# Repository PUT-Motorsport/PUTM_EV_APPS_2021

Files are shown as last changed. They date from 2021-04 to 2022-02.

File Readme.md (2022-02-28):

# Accelerator Pedal Position Sensor (APPS)

## Motivation

APPS handling is required by official FSG Rules according to T11.8 ([see](https://www.formulastudent.de/fileadmin/user_upload/all/2022/rules/FS-Rules_2022_v1.0.pdf#page=58)). APPS signals are system critical signals meaning that any implausibility between sensors or a failure should result in complete motor power shutdown.

## Pedal travel

* 0% - fully released
* 100% - fully applied

## Implausiblity

Implausibility is defined as a deviation of more than ten percentage points pedal travel
between any of the used APPSs. If it occurs for more than 100 ms the power to the motor must be immediately shut down.

## Platform

Software for APPS signal handling is developed using C++ for STM32 microcontroller.

## Program schematic

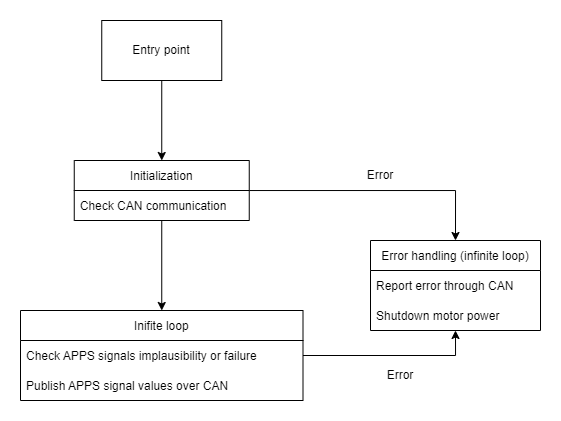
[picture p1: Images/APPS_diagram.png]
APPS diagram


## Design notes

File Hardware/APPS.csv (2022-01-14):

"Source:,""C:\Users\Patryk\Desktop\PUTM\APPS\PUTM_EV_APPS_2021\Hardware\APPS.kicad_sch"""
"Date:,""13.01.2022 20:09:16"""
"Tool:,""Eeschema (6.0.0)"""
"Generator:,""D:\KiCad\6.0\bin\scripting\plugins/bom_csv_grouped_by_value.py"""
"Component Count:,""62"""
Individual Components:
"Item,""Qty"",""Reference(s)"",""Value"",""LibPart"",""Footprint"",""Datasheet"""
","""",""C1"",""100nF"",""Device:C"",""Capacitor_SMD:C_0603_1608Metric_Pad1.08x0.95mm_HandSolder"",""~"""
","""",""C2"",""100nF"",""Device:C"",""Capacitor_SMD:C_0603_1608Metric_Pad1.08x0.95mm_HandSolder"",""~"""
","""",""C3"",""100nF"",""Device:C"",""Capacitor_SMD:C_0603_1608Metric_Pad1.08x0.95mm_HandSolder"",""~"""
","""",""C4"",""100nF"",""Device:C"",""Capacitor_SMD:C_0603_1608Metric_Pad1.08x0.95mm_HandSolder"",""~"""
","""",""C5"",""100nF"",""Device:C"",""Capacitor_SMD:C_0603_1608Metric_Pad1.08x0.95mm_HandSolder"",""~"""
","""",""C6"",""100nF"",""Device:C"",""Capacitor_SMD:C_0603_1608Metric_Pad1.08x0.95mm_HandSolder"",""~"""
","""",""C7"",""22pF"",""Device:C"",""Capacitor_SMD:C_0603_1608Metric_Pad1.08x0.95mm_HandSolder"",""~"""
","""",""C8"",""22pF"",""Device:C"",""Capacitor_SMD:C_0603_1608Metric_Pad1.08x0.95mm_HandSolder"",""~"""
","""",""C12"",""100nF"",""Device:C"",""Capacitor_SMD:C_0603_1608Metric_Pad1.08x0.95mm_HandSolder"",""~"""
","""",""C13"",""100nF"",""Device:C"",""Capacitor_SMD:C_0603_1608Metric_Pad1.08x0.95mm_HandSolder"",""~"""
","""",""C14"",""100nF"",""Device:C"",""Capacitor_SMD:C_0603_1608Metric_Pad1.08x0.95mm_HandSolder"",""~"""
","""",""C15"",""100nF"",""Device:C"",""Capacitor_SMD:C_0603_1608Metric_Pad1.08x0.95mm_HandSolder"",""~"""
","""",""C16"",""100nF"",""Device:C"",""Capacitor_SMD:C_0603_1608Metric_Pad1.08x0.95mm_HandSolder"",""~"""
","""",""C17"",""100nF"",""Device:C"",""Capacitor_SMD:C_0603_1608Metric_Pad1.08x0.95mm_HandSolder"",""~"""
","""",""C18"",""100nF"",""Device:C"",""Capacitor_SMD:C_0603_1608Metric_Pad1.08x0.95mm_HandSolder"",""~"""
","""",""C19"",""100n"",""Device:C"",""Capacitor_SMD:C_0603_1608Metric_Pad1.08x0.95mm_HandSolder"",""~"""
","""",""C20"",""100n"",""Device:C"",""Capacitor_SMD:C_0603_1608Metric_Pad1.08x0.95mm_HandSolder"",""~"""
","""",""D1"",""LED"",""Device:LED"",""LED_SMD:LED_0603_1608Metric_Pad1.05x0.95mm_HandSolder"",""~"""
","""",""D2"",""LED"",""Device:LED"",""LED_SMD:LED_0603_1608Metric_Pad1.05x0.95mm_HandSolder"",""~"""
","""",""D3"",""LED"",""Device:LED"",""LED_SMD:LED_0603_1608Metric_Pad1.05x0.95mm_HandSolder"",""~"""
","""",""D4"",""LED"",""Device:LED"",""LED_SMD:LED_0603_1608Metric_Pad1.05x0.95mm_HandSolder"",""~"""
","""",""D5"",""D_TVS"",""Device:D_TVS"",""Diode_SMD:D_0603_1608Metric_Pad1.05x0.95mm_HandSolder"",""~"""
","""",""D6"",""D_TVS"",""Device:D_TVS"",""Diode_SMD:D_0603_1608Metric_Pad1.05x0.95mm_HandSolder"",""~"""
","""",""D9"",""PESD2CAN.215"",""Device:D_TVS_x2_AAC"",""Package_TO_SOT_SMD:SOT-23"","""""
","""",""D10"",""DIODE"",""pspice:DIODE"",""Diode_SMD:D_SMB"",""~"""
","""",""F2"",""Fuse"",""Device:Fuse"",""Fuse:Fuse_2010_5025Metric"",""~"""
","""",""F3"",""Fuse"",""Device:Fuse"",""Fuse:Fuse_2010_5025Metric"",""~"""
","""",""J4"",""Sygnały"",""conn_02x20_odd_even:Conn_02x20_Odd_Even"",""Connector_PinSocket_2.54mm:PinSocket_2x20_P2.54mm_Vertical"","""""
","""",""J5"",""Diagnostyka"",""conn_02x10_odd_even:Conn_02x10_Odd_Even"",""Connector_PinSocket_2.54mm:PinSocket_2x10_P2.54mm_Vertical"","""""
","""",""J8"",""Zasilanie+CAN"",""conn_02x10_odd_even:Conn_02x10_Odd_Even"",""Connector_PinSocket_2.54mm:PinSocket_2x10_P2.54mm_Vertical"","""""
","""",""JP1"",""Jumper_NC_Small"",""Device:Jumper_NC_Small"",""Connector_PinHeader_2.54mm:PinHeader_1x02_P2.54mm_Vertical"","""""
","""",""K1"",""FINDER-30.22"",""Relay:FINDER-30.22"",""Relay_THT:Relay_DPDT_Finder_30.22"",""http://gfinder.findernet.com/assets/Series/354/S30EN.pdf"""
","""",""L1"",""10u"",""Device:L"",""Inductor_SMD:L_0805_2012Metric"",""~"""
","""",""Q1"",""BSS138"",""Transistor_FET:BSS138"",""Package_TO_SOT_SMD:SOT-23"",""https://www.fairchildsemi.com/datasheets/BS/BSS138.pdf"""
","""",""R1"",""10k"",""Device:R_Small"",""Resistor_SMD:R_0603_1608Metric_Pad0.98x0.95mm_HandSolder"",""~"""
","""",""R2"",""10k"",""Device:R_Small"",""Resistor_SMD:R_0603_1608Metric_Pad0.98x0.95mm_HandSolder"",""~"""
","""",""R3"",""300R"",""Device:R"",""Resistor_SMD:R_0603_1608Metric_Pad0.98x0.95mm_HandSolder"",""~"""
","""",""R4"",""300R"",""Device:R"",""Resistor_SMD:R_0603_1608Metric_Pad0.98x0.95mm_HandSolder"",""~"""
","""",""R5"",""300R"",""Device:R"",""Resistor_SMD:R_0603_1608Metric_Pad0.98x0.95mm_HandSolder"",""~"""
","""",""R6"",""300R"",""Device:R"",""Resistor_SMD:R_0603_1608Metric_Pad0.98x0.95mm_HandSolder"",""~"""
","""",""R8"",""120R"",""Device:R_Small"",""Resistor_SMD:R_0603_1608Metric_Pad0.98x0.95mm_HandSolder"",""~"""
","""",""R9"",""100R"",""Device:R_Small"",""Resistor_SMD:R_0603_1608Metric_Pad0.98x0.95mm_HandSolder"",""~"""
","""",""R10"",""10k"",""Device:R_Small"",""Resistor_SMD:R_0603_1608Metric_Pad0.98x0.95mm_HandSolder"",""~"""
","""",""R11"",""220R"",""Device:R"",""Resistor_SMD:R_1206_3216Metric"",""~"""
","""",""R12"",""4k7"",""Device:R"",""Resistor_SMD:R_0603_1608Metric_Pad0.98x0.95mm_HandSolder"",""~"""
","""",""R13"",""0R"",""Device:R"",""Resistor_SMD:R_1206_3216Metric"",""~"""
","""",""R14"",""0R"",""Device:R"",""Resistor_SMD:R_0603_1608Metric_Pad0.98x0.95mm_HandSolder"",""~"""
","""",""R15"",""0R"",""Device:R"",""Resistor_SMD:R_1206_3216Metric"",""~"""
","""",""R16"",""4k7"",""Device:R"",""Resistor_SMD:R_0603_1608Metric_Pad0.98x0.95mm_HandSolder"",""~"""
","""",""R17"",""220R"",""Device:R"",""Resistor_SMD:R_1206_3216Metric"",""~"""
","""",""R18"",""0R"",""Device:R"",""Resistor_SMD:R_0603_1608Metric_Pad0.98x0.95mm_HandSolder"",""~"""
","""",""R23"",""100k"",""Device:R_Small"",""Resistor_SMD:R_0603_1608Metric_Pad0.98x0.95mm_HandSolder"",""~"""
","""",""R24"",""100k"",""Device:R_Small"",""Resistor_SMD:R_0603_1608Metric_Pad0.98x0.95mm_HandSolder"",""~"""
","""",""SW1"",""SW_Push"",""Switch:SW_Push"",""Button_Switch_THT:SW_PUSH_6mm"",""~"""
","""",""U1"",""STM32L4P5RET6"",""STM32L4P5RET6:STM32L4P5RET6"",""Package_QFP:LQFP-64_10x10mm_P0.5mm"","""""
","""",""U3"",""LM1117-3.3"",""Regulator_Linear:LM1117-3.3"",""Package_TO_SOT_SMD:SOT-223-3_TabPin2"",""http://www.ti.com/lit/ds/symlink/lm1117.pdf"""
","""",""U4"",""LM1117-3.3"",""Regulator_Linear:LM1117-3.3"",""Package_TO_SOT_SMD:SOT-223-3_TabPin2"",""http://www.ti.com/lit/ds/symlink/lm1117.pdf"""
","""",""U5"",""LM1117-3.3"",""Regulator_Linear:LM1117-3.3"",""Package_TO_SOT_SMD:SOT-223-3_TabPin2"",""http://www.ti.com/lit/ds/symlink/lm1117.pdf"""
","""",""U6"",""MCP2562-H-SN"",""Interface_CAN_LIN:MCP2562-H-SN"",""Package_SO:SOIC-8_3.9x4.9mm_P1.27mm"",""http://ww1.microchip.com/downloads/en/DeviceDoc/25167A.pdf"""
","""",""U7"",""MCP6001-OT"",""Amplifier_Operational:MCP6001-OT"",""Package_TO_SOT_SMD:SOT-23-5"",""http://ww1.microchip.com/downloads/en/DeviceDoc/21733j.pdf"""
","""",""U8"",""MCP6001-OT"",""Amplifier_Operational:MCP6001-OT"",""Package_TO_SOT_SMD:SOT-23-5"",""http://ww1.microchip.com/downloads/en/DeviceDoc/21733j.pdf"""
","""",""Y1"",""Crystal_GND24"",""Device:Crystal_GND24"",""Crystal:Crystal_SMD_2520-4Pin_2.5x2.0mm"",""https://abracon.com/Resonators/abm8.pdf"""
Collated Components:
"Item,""Qty"",""Reference(s)"",""Value"",""LibPart"",""Footprint"",""Datasheet"""
"1,""13"",""C1, C2, C3, C4, C5, C6, C12, C13, C14, C15, C16, C17, C18"",""100nF"",""Device:C"",""Capacitor_SMD:C_0603_1608Metric_Pad1.08x0.95mm_HandSolder"",""~"""
"2,""2"",""C7, C8"",""22pF"",""Device:C"",""Capacitor_SMD:C_0603_1608Metric_Pad1.08x0.95mm_HandSolder"",""~"""
"3,""2"",""C19, C20"",""100n"",""Device:C"",""Capacitor_SMD:C_0603_1608Metric_Pad1.08x0.95mm_HandSolder"",""~"""
"4,""4"",""D1, D2, D3, D4"",""LED"",""Device:LED"",""LED_SMD:LED_0603_1608Metric_Pad1.05x0.95mm_HandSolder"",""~"""
"5,""2"",""D5, D6"",""D_TVS"",""Device:D_TVS"",""Diode_SMD:D_0603_1608Metric_Pad1.05x0.95mm_HandSolder"",""~"""
"6,""1"",""D9"",""PESD2CAN.215"",""Device:D_TVS_x2_AAC"",""Package_TO_SOT_SMD:SOT-23"","""""
"7,""1"",""D10"",""DIODE"",""pspice:DIODE"",""Diode_SMD:D_SMB"",""~"""
"8,""2"",""F2, F3"",""Fuse"",""Device:Fuse"",""Fuse:Fuse_2010_5025Metric"",""~"""
"9,""1"",""J4"",""Sygnały"",""conn_02x20_odd_even:Conn_02x20_Odd_Even"",""Connector_PinSocket_2.54mm:PinSocket_2x20_P2.54mm_Vertical"","""""
"10,""1"",""J5"",""Diagnostyka"",""conn_02x10_odd_even:Conn_02x10_Odd_Even"",""Connector_PinSocket_2.54mm:PinSocket_2x10_P2.54mm_Vertical"","""""
"11,""1"",""J8"",""Zasilanie+CAN"",""conn_02x10_odd_even:Conn_02x10_Odd_Even"",""Connector_PinSocket_2.54mm:PinSocket_2x10_P2.54mm_Vertical"","""""
"12,""1"",""JP1"",""Jumper_NC_Small"",""Device:Jumper_NC_Small"",""Connector_PinHeader_2.54mm:PinHeader_1x02_P2.54mm_Vertical"","""""
"13,""1"",""K1"",""FINDER-30.22"",""Relay:FINDER-30.22"",""Relay_THT:Relay_DPDT_Finder_30.22"",""http://gfinder.findernet.com/assets/Series/354/S30EN.pdf"""
"14,""1"",""L1"",""10u"",""Device:L"",""Inductor_SMD:L_0805_2012Metric"",""~"""
"15,""1"",""Q1"",""BSS138"",""Transistor_FET:BSS138"",""Package_TO_SOT_SMD:SOT-23"",""https://www.fairchildsemi.com/datasheets/BS/BSS138.pdf"""
"16,""3"",""R1, R2, R10"",""10k"",""Device:R_Small"",""Resistor_SMD:R_0603_1608Metric_Pad0.98x0.95mm_HandSolder"",""~"""
"17,""4"",""R3, R4, R5, R6"",""300R"",""Device:R"",""Resistor_SMD:R_0603_1608Metric_Pad0.98x0.95mm_HandSolder"",""~"""
"18,""1"",""R8"",""120R"",""Device:R_Small"",""Resistor_SMD:R_0603_1608Metric_Pad0.98x0.95mm_HandSolder"",""~"""
"19,""1"",""R9"",""100R"",""Device:R_Small"",""Resistor_SMD:R_0603_1608Metric_Pad0.98x0.95mm_HandSolder"",""~"""
"20,""2"",""R11, R17"",""220R"",""Device:R"",""Resistor_SMD:R_1206_3216Metric"",""~"""
"21,""2"",""R12, R16"",""4k7"",""Device:R"",""Resistor_SMD:R_0603_1608Metric_Pad0.98x0.95mm_HandSolder"",""~"""
"22,""2"",""R13, R15"",""0R"",""Device:R"",""Resistor_SMD:R_1206_3216Metric"",""~"""
"23,""2"",""R14, R18"",""0R"",""Device:R"",""Resistor_SMD:R_0603_1608Metric_Pad0.98x0.95mm_HandSolder"",""~"""
"24,""2"",""R23, R24"",""100k"",""Device:R_Small"",""Resistor_SMD:R_0603_1608Metric_Pad0.98x0.95mm_HandSolder"",""~"""
"25,""1"",""SW1"",""SW_Push"",""Switch:SW_Push"",""Button_Switch_THT:SW_PUSH_6mm"",""~"""
"26,""1"",""U1"",""STM32L4P5RET6"",""STM32L4P5RET6:STM32L4P5RET6"",""Package_QFP:LQFP-64_10x10mm_P0.5mm"","""""
"27,""3"",""U3, U4, U5"",""LM1117-3.3"",""Regulator_Linear:LM1117-3.3"",""Package_TO_SOT_SMD:SOT-223-3_TabPin2"",""http://www.ti.com/lit/ds/symlink/lm1117.pdf"""
"28,""1"",""U6"",""MCP2562-H-SN"",""Interface_CAN_LIN:MCP2562-H-SN"",""Package_SO:SOIC-8_3.9x4.9mm_P1.27mm"",""http://ww1.microchip.com/downloads/en/DeviceDoc/25167A.pdf"""
"29,""2"",""U7, U8"",""MCP6001-OT"",""Amplifier_Operational:MCP6001-OT"",""Package_TO_SOT_SMD:SOT-23-5"",""http://ww1.microchip.com/downloads/en/DeviceDoc/21733j.pdf"""
"30,""1"",""Y1"",""Crystal_GND24"",""Device:Crystal_GND24"",""Crystal:Crystal_SMD_2520-4Pin_2.5x2.0mm"",""https://abracon.com/Resonators/abm8.pdf"""

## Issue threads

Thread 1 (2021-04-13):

Check if sensors are connected

KwiatPiotr, 2021-04-13:
Both sensors have to be connected if any of them is not disable device and send 0 as measurement.

KwiatPiotr, 2021-04-29:
Done

Closed 2021-04-29.

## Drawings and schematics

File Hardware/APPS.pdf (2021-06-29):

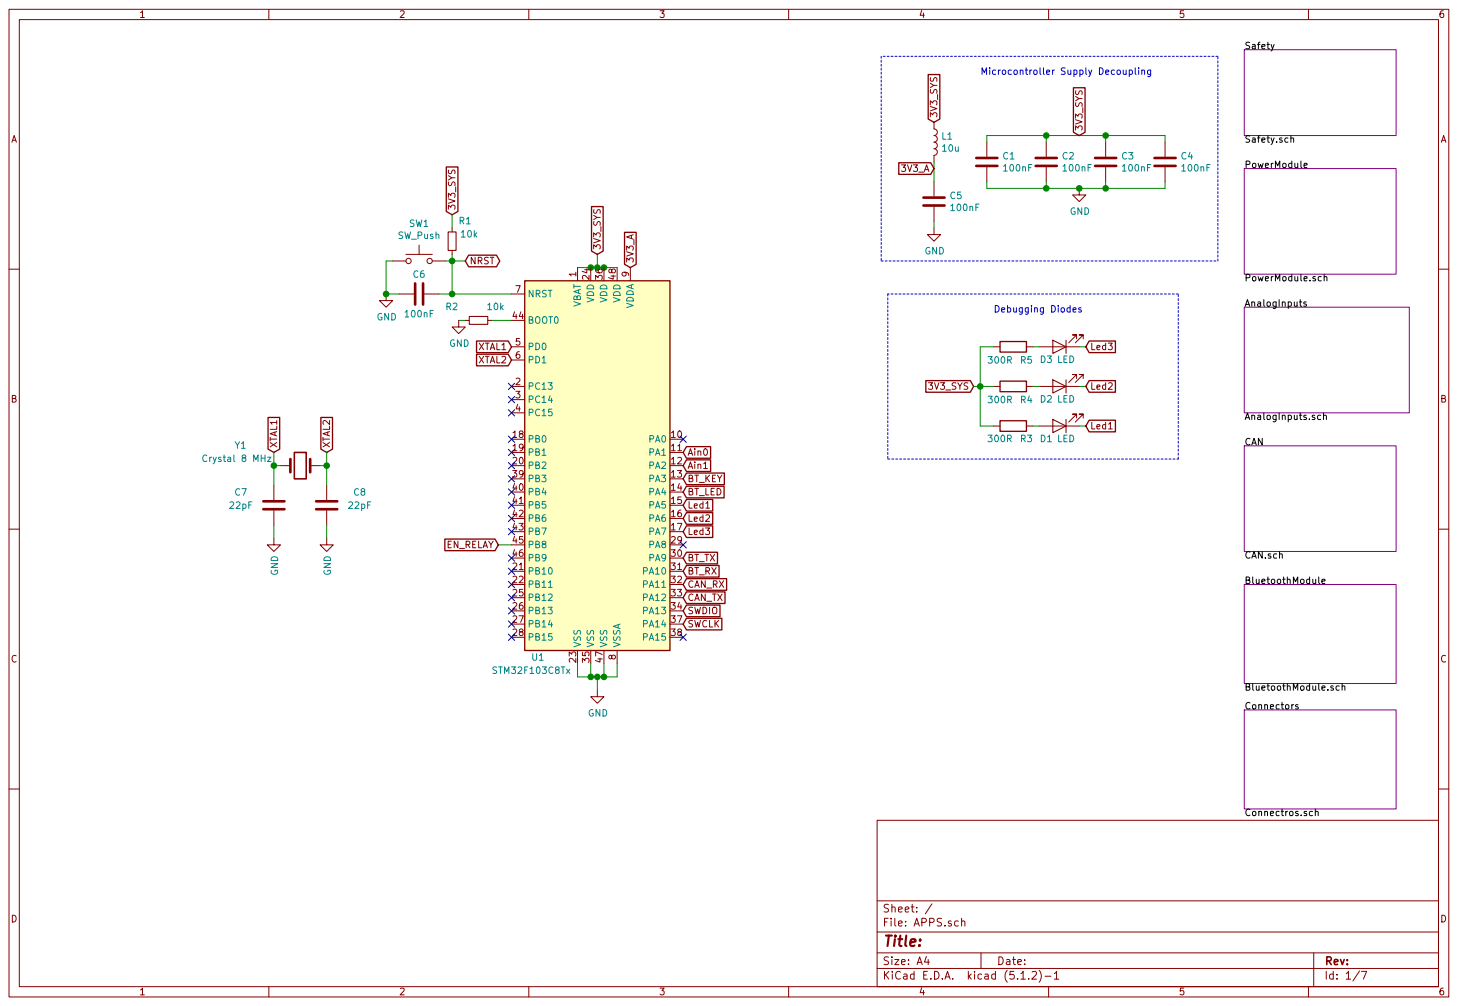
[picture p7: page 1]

Safety
PowerModule PowerModule.sch CAN

Led1
BluetoothModule BluetoothModule.sch Connectors Connectros.sch

Id: 1/7 Title: File: APPS.sch Sheet: /

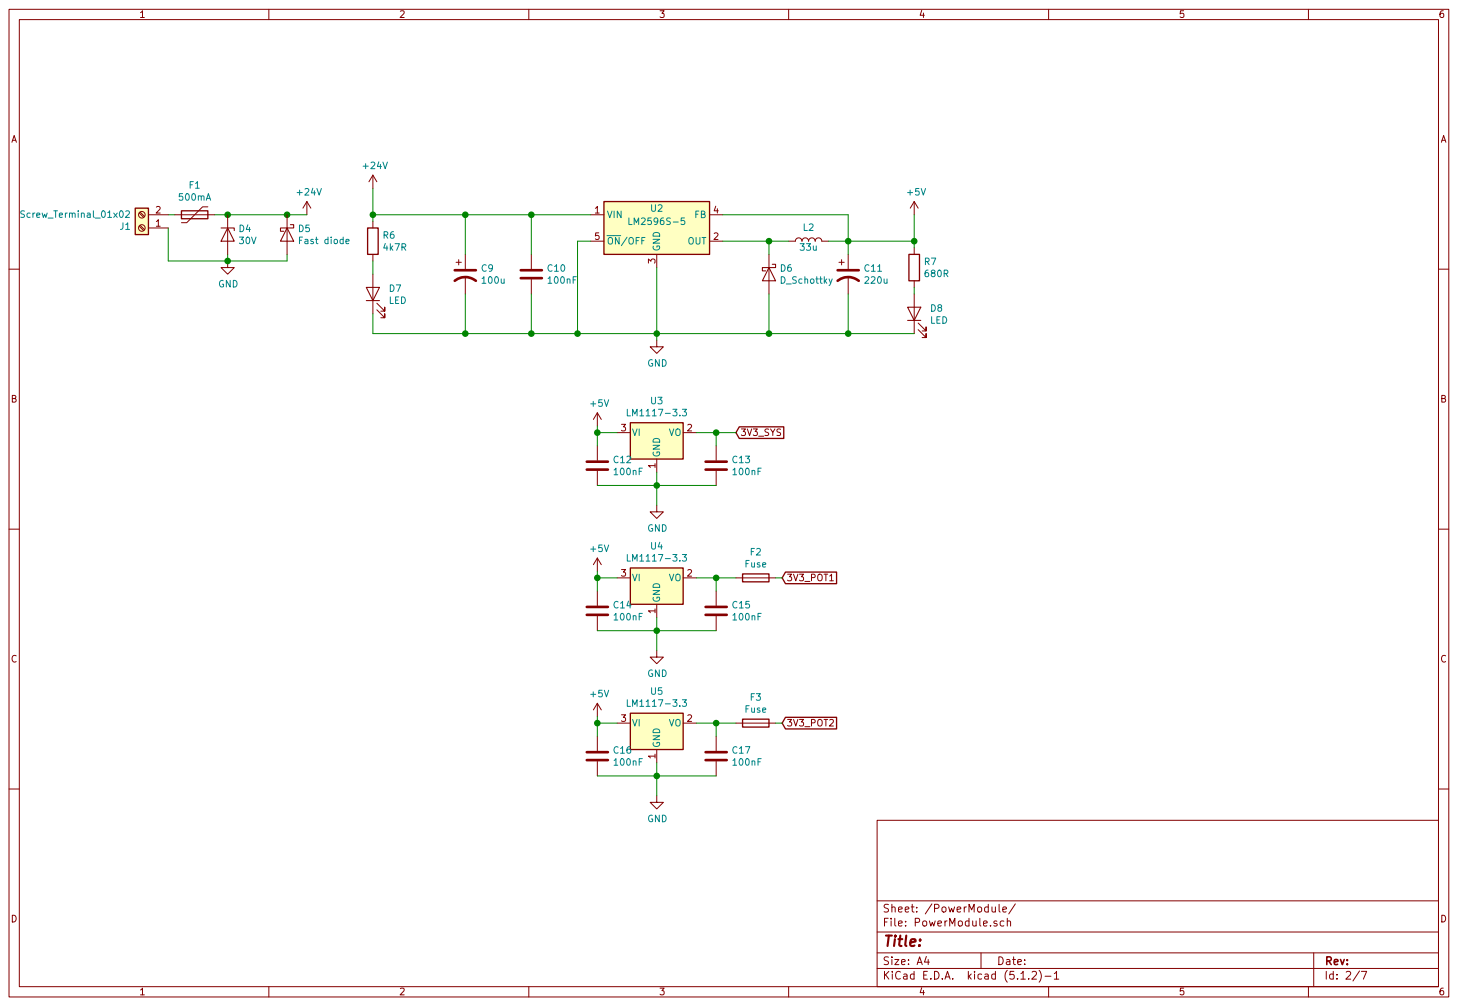
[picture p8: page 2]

Id: 2/7 Title: File: PowerModule.sch Sheet: /PowerModule/

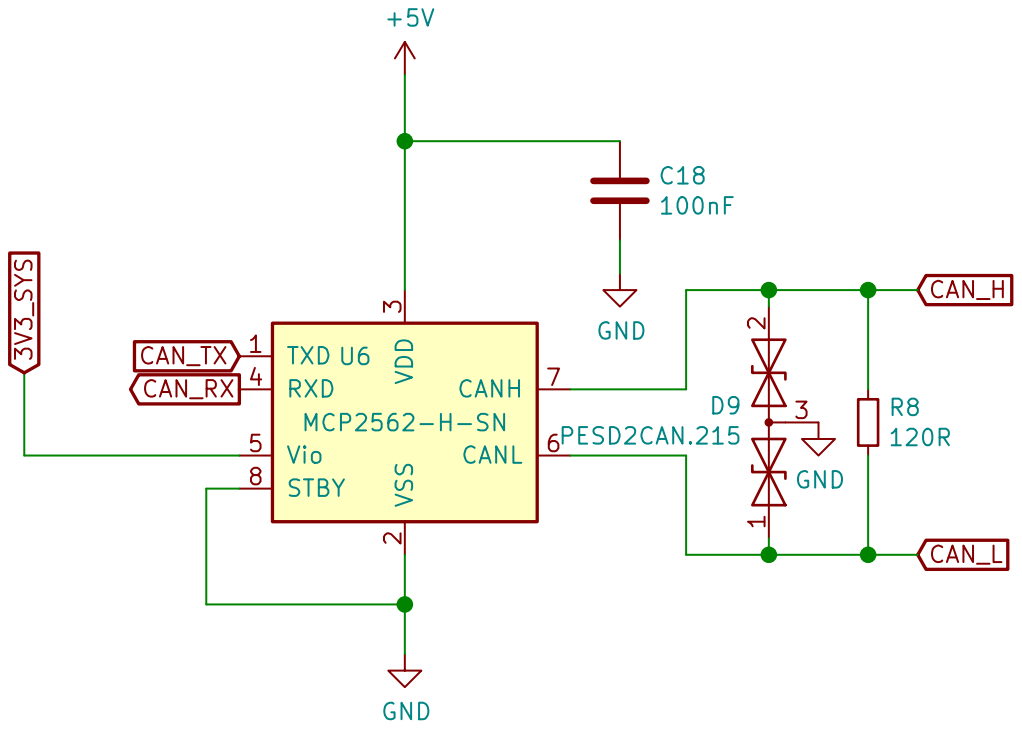
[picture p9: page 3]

3 RXD 4 Vio 5 CANL 6 CANH 7 STBY 8 U6 MCP2562-H-SN GND GND

Id: 3/7 Title: File: CAN.sch Sheet: /CAN/

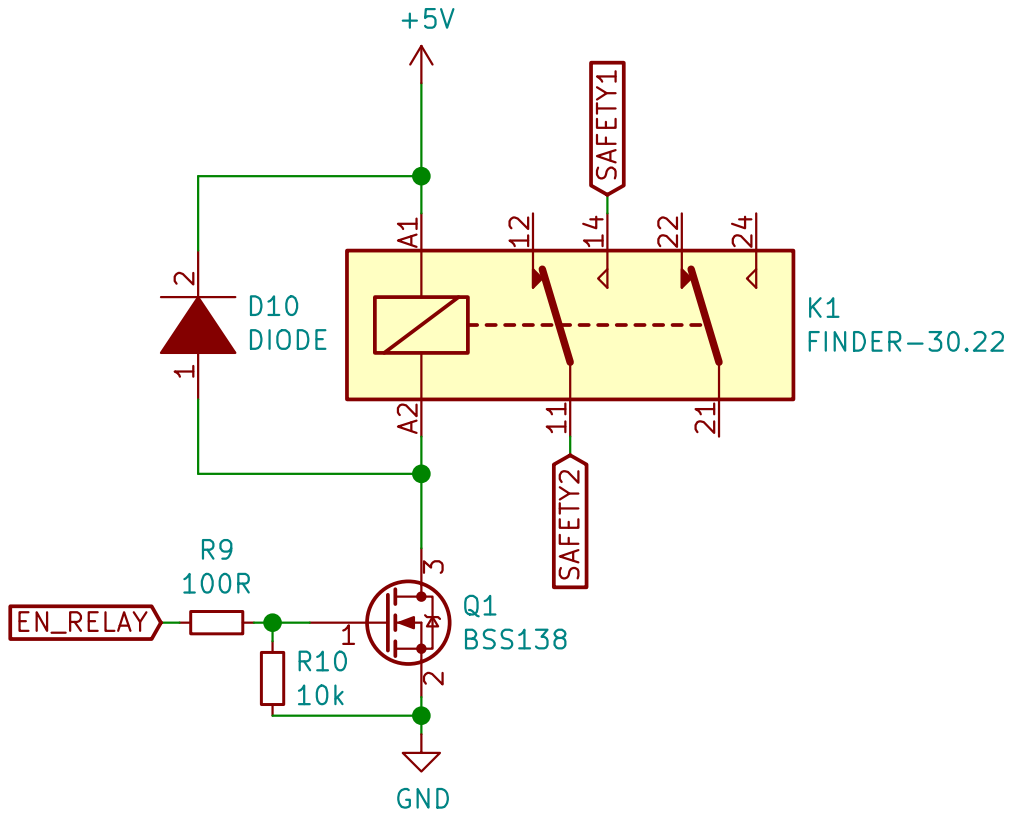
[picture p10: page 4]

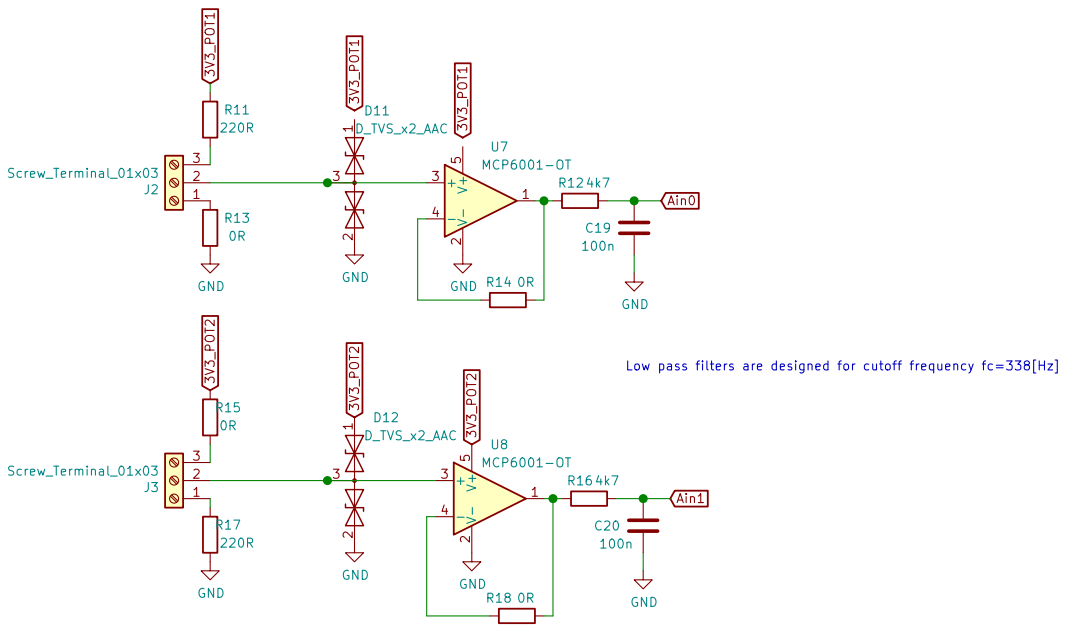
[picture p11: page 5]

Low pass filters are designed for cutoff frequency fc=338[Hz]

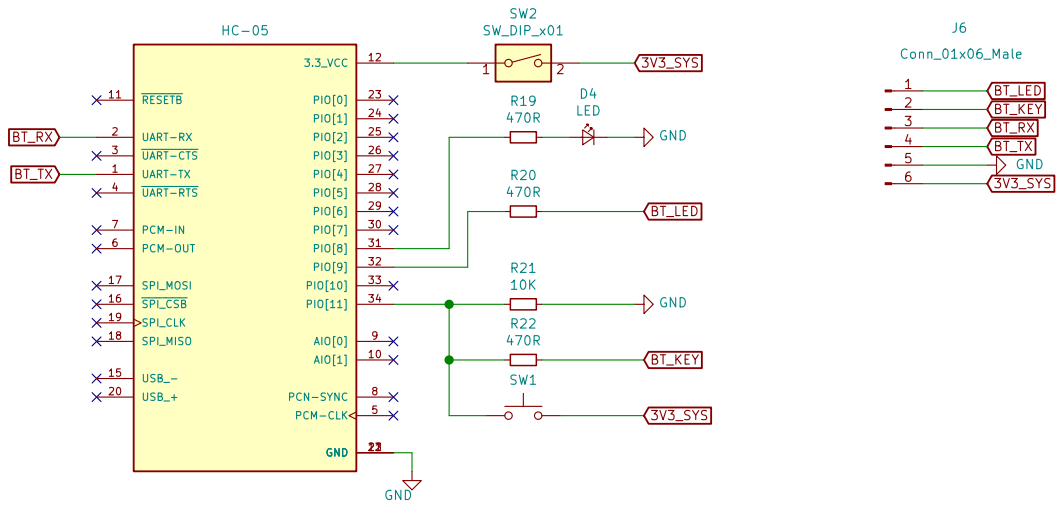
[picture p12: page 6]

Id: 6/7 Title: File: BluetoothModule.sch Sheet: /BluetoothModule/

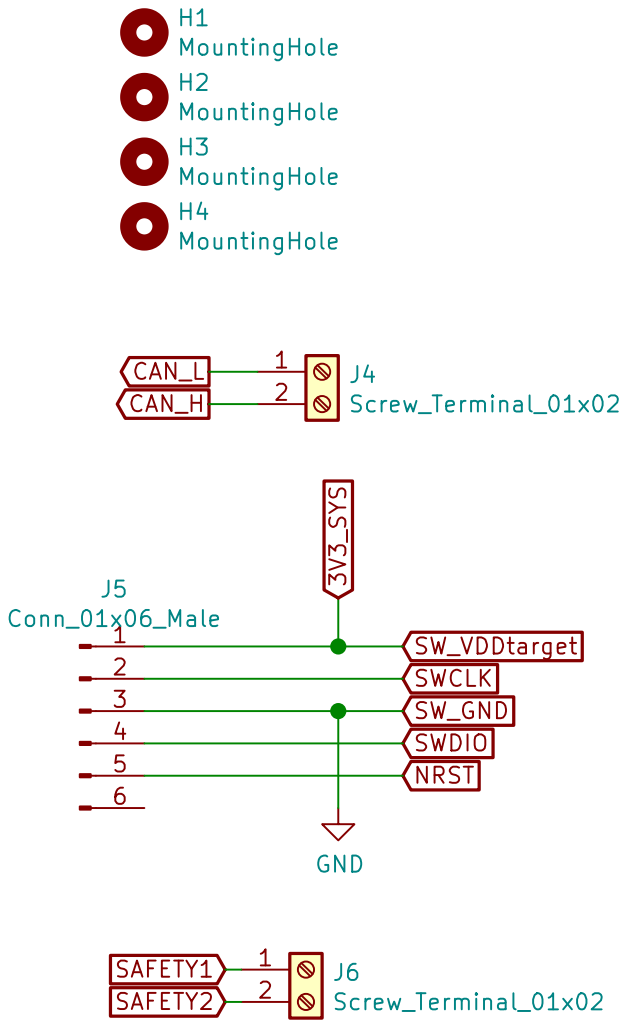
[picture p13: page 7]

Id: 7/7 Title: File: Connectros.sch Sheet: /Connectors/ 12

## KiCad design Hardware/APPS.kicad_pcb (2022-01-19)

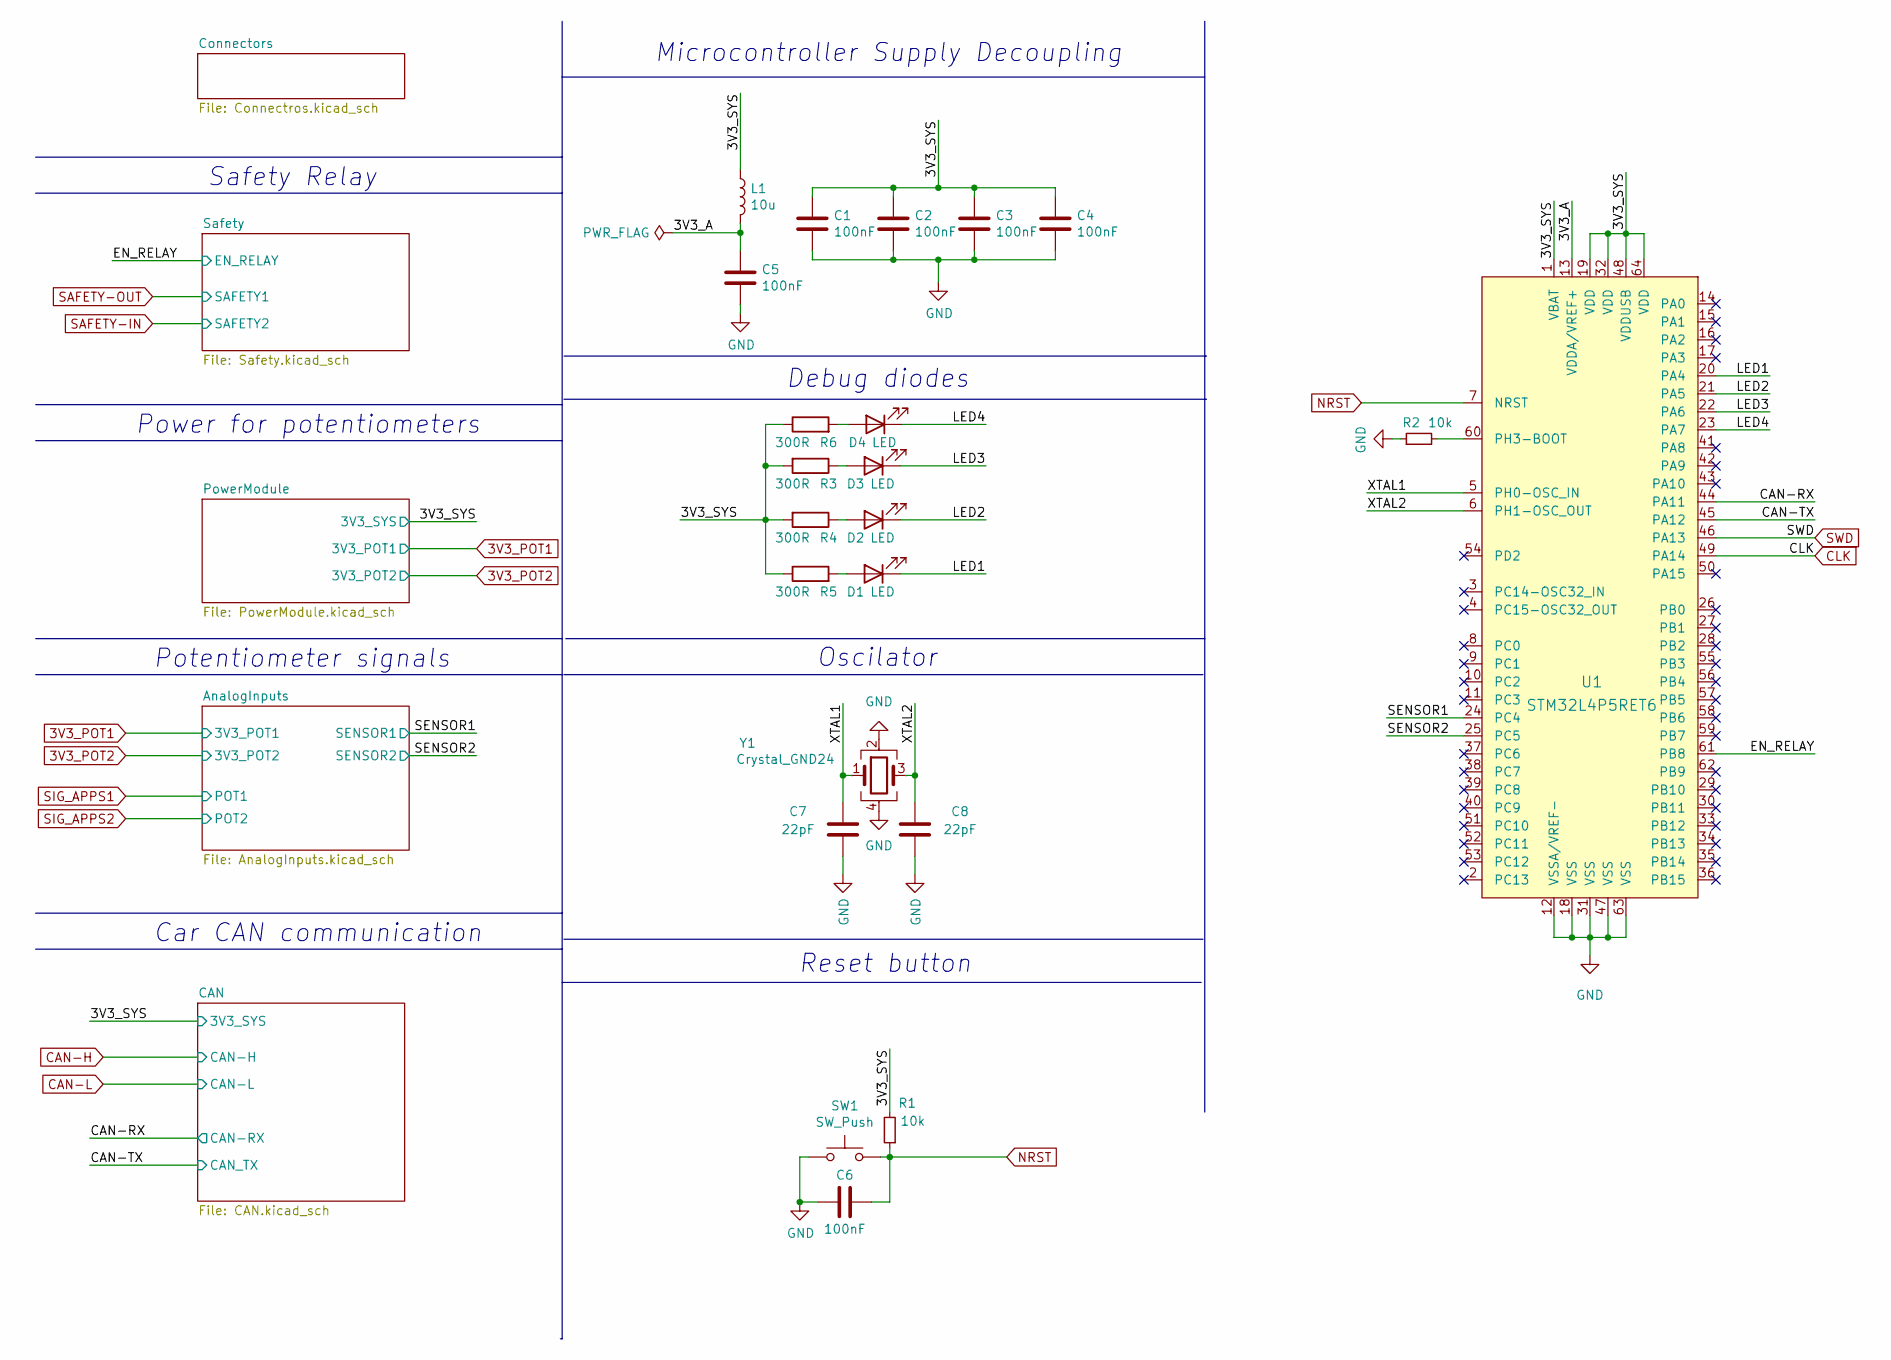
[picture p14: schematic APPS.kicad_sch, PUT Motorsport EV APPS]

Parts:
C1, C2, C3, C4, C5, C6: 100nF; C_0603_1608Metric_Pad1.08x0.95mm_HandSolder
C7, C8: 22pF; C_0603_1608Metric_Pad1.08x0.95mm_HandSolder
D1, D2, D3, D4: LED; LED_0603_1608Metric_Pad1.05x0.95mm_HandSolder
L1: 10u; L_0805_2012Metric
R1, R2: 10k; R_0603_1608Metric_Pad0.98x0.95mm_HandSolder
R3, R4, R5, R6: 300R; R_0603_1608Metric_Pad0.98x0.95mm_HandSolder
SW1: SW_Push; SW_PUSH_6mm
U1: STM32L4P5RET6; LQFP-64_10x10mm_P0.5mm
Y1: Crystal_GND24; Crystal_SMD_2520-4Pin_2.5x2.0mm

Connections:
/3V3_A: C5.1, L1.2, U1.13 (VDDA/VREF+)
/3V3_SYS: C1.1, C2.1, C3.1, C4.1, L1.1, R1.2, R3.2, R4.2, R5.1, R6.1, U1.1 (VBAT), U1.19 (VDD), U1.32 (VDD), U1.48 (VDDUSB), U1.64 (VDD); also elsewhere on the board
/CAN-RX: U1.44 (PA11); also elsewhere on the board
/CAN-TX: U1.45 (PA12); also elsewhere on the board
/EN_RELAY: U1.61 (PB8); also elsewhere on the board
/LED1: D1.1 (K), U1.20 (PA4)
/LED2: D2.1 (K), U1.21 (PA5)
/LED3: D3.1 (K), U1.22 (PA6)
/LED4: D4.1 (K), U1.23 (PA7)
/SENSOR1: U1.24 (PC4); also elsewhere on the board
/SENSOR2: U1.25 (PC5); also elsewhere on the board
/XTAL1: C7.1, U1.5 (PH0-OSC_IN), Y1.1
/XTAL2: C8.1, U1.6 (PH1-OSC_OUT), Y1.3
CLK: U1.49 (PA14); also elsewhere on the board
GND: C1.2, C2.2, C3.2, C4.2, C5.2, C6.2, C7.2, C8.2, R2.1, SW1.1, U1.12 (VSSA/VREF-), U1.18 (VSS), U1.31 (VSS), U1.47 (VSS), U1.63 (VSS), Y1.2, Y1.4; also elsewhere on the board
NRST: C6.1, R1.1, SW1.2, U1.7 (NRST); also elsewhere on the board
unnamed: D1.2 (A), R5.2
unnamed: D2.2 (A), R4.1
unnamed: D3.2 (A), R3.1
unnamed: D4.2 (A), R6.2
unnamed: R2.2, U1.60 (PH3-BOOT)
SWD: U1.46 (PA13); also elsewhere on the board

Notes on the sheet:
Power for potentiometers
Oscilator
Reset button
Safety Relay
Microcontroller Supply Decoupling
Debug diodes
Potentiometer signals
Car CAN communication

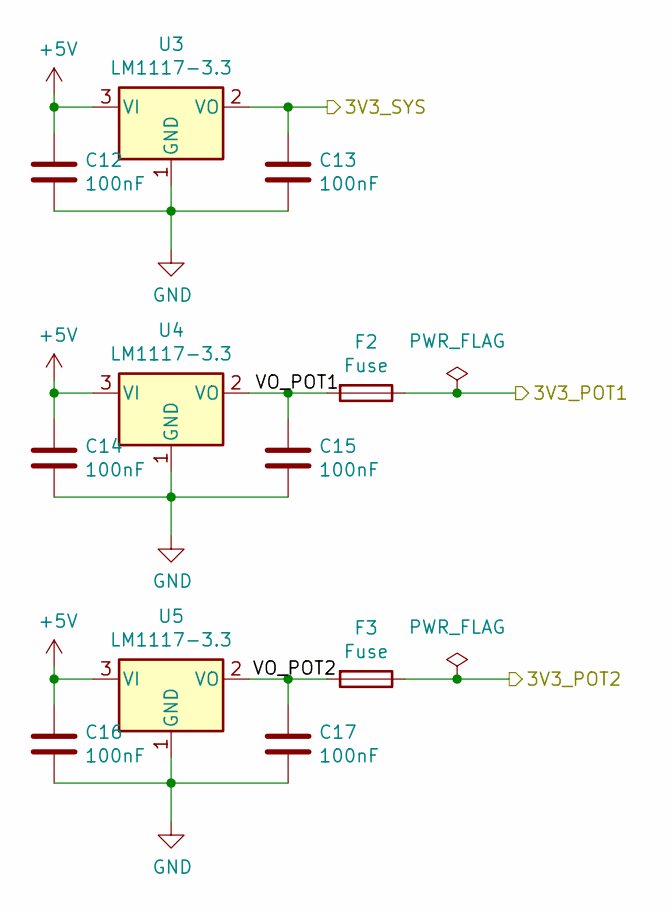
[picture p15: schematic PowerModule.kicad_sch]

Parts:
C12, C13, C14, C15, C16, C17: 100nF; C_0603_1608Metric_Pad1.08x0.95mm_HandSolder
F2, F3: Fuse; Fuse_2010_5025Metric
U3, U4, U5: LM1117-3.3; SOT-223-3_TabPin2

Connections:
3V3_POT1: F2.1; also elsewhere on the board
3V3_POT2: F3.1; also elsewhere on the board
+5V: C12.1, C14.1, C16.1, U3.3 (VI), U4.3 (VI), U5.3 (VI); also elsewhere on the board
/3V3_SYS: C13.1, U3.2 (VO); also elsewhere on the board
/PowerModule/VO_POT1: C15.1, F2.2, U4.2 (VO)
/PowerModule/VO_POT2: C17.1, F3.2, U5.2 (VO)
GND: C12.2, C13.2, C14.2, C15.2, C16.2, C17.2, U3.1 (GND), U4.1 (GND), U5.1 (GND); also elsewhere on the board

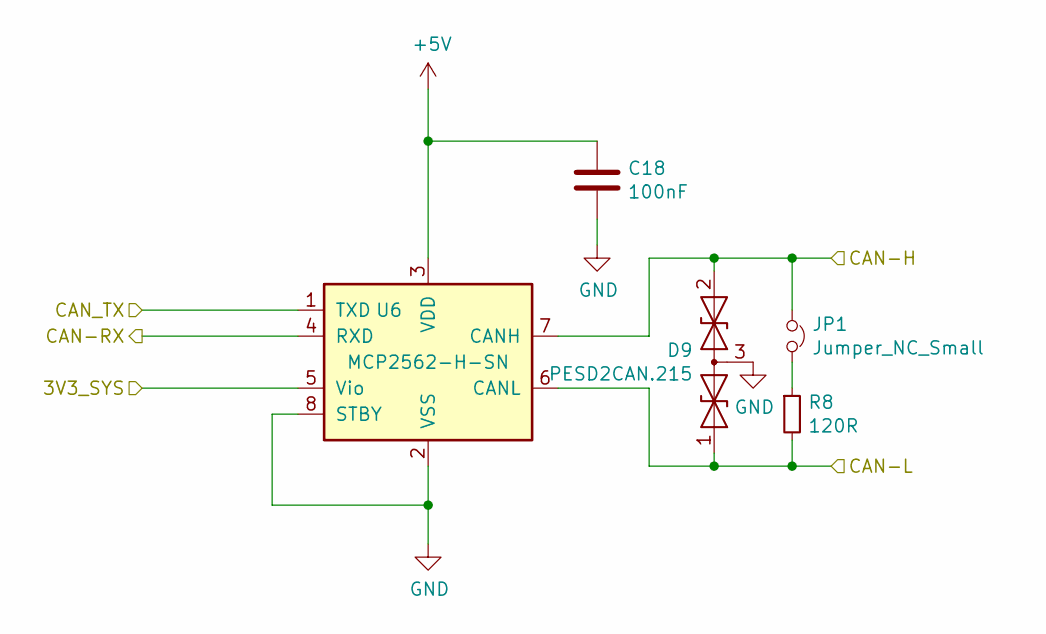
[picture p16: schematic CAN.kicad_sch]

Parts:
C18: 100nF; C_0603_1608Metric_Pad1.08x0.95mm_HandSolder
D9: PESD2CAN.215; SOT-23
JP1: Jumper_NC_Small; PinHeader_1x02_P2.54mm_Vertical
R8: 120R; R_0603_1608Metric_Pad0.98x0.95mm_HandSolder
U6: MCP2562-H-SN; SOIC-8_3.9x4.9mm_P1.27mm

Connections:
+5V: C18.1, U6.3 (VDD); also elsewhere on the board
/3V3_SYS: U6.5 (Vio); also elsewhere on the board
/CAN-RX: U6.4 (RXD); also elsewhere on the board
/CAN-TX: U6.1 (TXD); also elsewhere on the board
CAN-H: D9.2 (A2), JP1.1, U6.7 (CANH); also elsewhere on the board
CAN-L: D9.1 (A1), R8.2, U6.6 (CANL); also elsewhere on the board
GND: C18.2, D9.3 (common), U6.2 (VSS), U6.8 (STBY); also elsewhere on the board
unnamed: JP1.2, R8.1

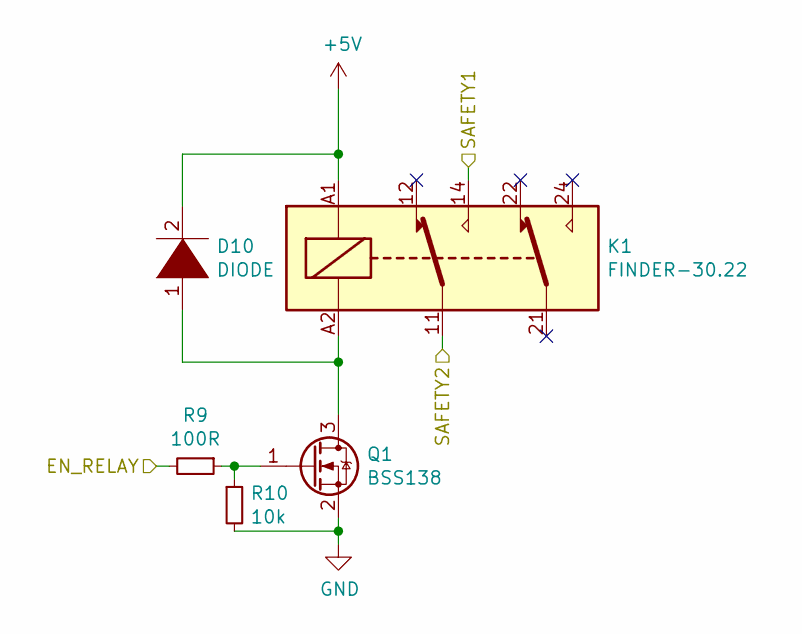
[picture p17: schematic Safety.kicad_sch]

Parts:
D10: DIODE; D_SMB
K1: FINDER-30.22; Relay_DPDT_Finder_30.22
Q1: BSS138; SOT-23
R9: 100R; R_0603_1608Metric_Pad0.98x0.95mm_HandSolder
R10: 10k; R_0603_1608Metric_Pad0.98x0.95mm_HandSolder

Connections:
+5V: D10.2 (A), K1.A1; also elsewhere on the board
/EN_RELAY: R9.2; also elsewhere on the board
GND: Q1.2 (S), R10.2; also elsewhere on the board
unnamed: D10.1 (K), K1.A2, Q1.3 (D)
unnamed: Q1.1 (G), R9.1, R10.1
SAFETY-IN: K1.11; also elsewhere on the board
SAFETY-OUT: K1.14; also elsewhere on the board

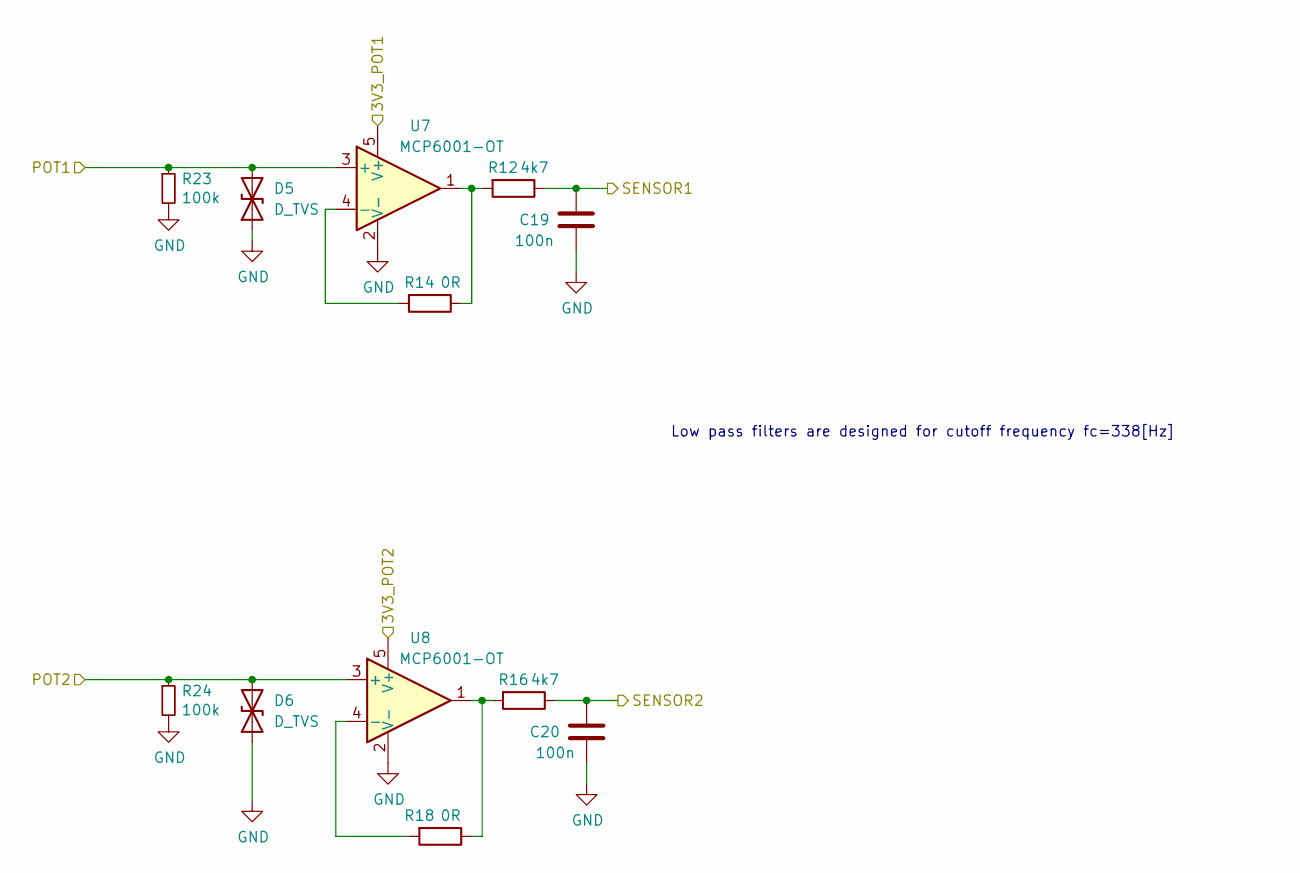
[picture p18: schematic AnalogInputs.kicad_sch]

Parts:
C19, C20: 100n; C_0603_1608Metric_Pad1.08x0.95mm_HandSolder
D5, D6: D_TVS; D_0603_1608Metric_Pad1.05x0.95mm_HandSolder
R12, R16: 4k7; R_0603_1608Metric_Pad0.98x0.95mm_HandSolder
R14, R18: 0R; R_0603_1608Metric_Pad0.98x0.95mm_HandSolder
R23, R24: 100k; R_0603_1608Metric_Pad0.98x0.95mm_HandSolder
U7, U8: MCP6001-OT; SOT-23-5

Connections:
3V3_POT1: U7.5 (V+); also elsewhere on the board
3V3_POT2: U8.5 (V+); also elsewhere on the board
/SENSOR1: C19.1, R12.1; also elsewhere on the board
/SENSOR2: C20.1, R16.1; also elsewhere on the board
GND: C19.2, C20.2, D5.1 (A1), D6.1 (A1), R23.2, R24.2, U7.2 (V-), U8.2 (V-); also elsewhere on the board
unnamed: R12.2, R14.1, U7.1
unnamed: R14.2, U7.4 (-)
unnamed: R16.2, R18.1, U8.1
unnamed: R18.2, U8.4 (-)
SIG_APPS1: D5.2 (A2), R23.1, U7.3 (+); also elsewhere on the board
SIG_APPS2: D6.2 (A2), R24.1, U8.3 (+); also elsewhere on the board

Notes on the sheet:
Low pass filters are designed for cutoff frequency fc=338[Hz]

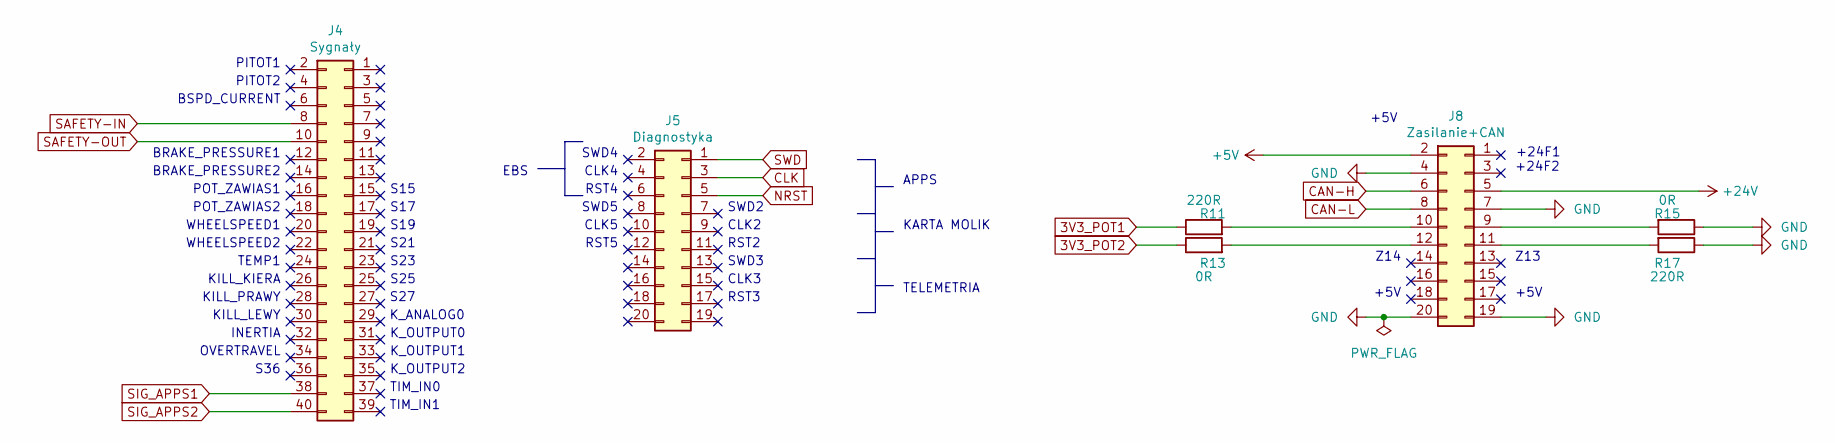
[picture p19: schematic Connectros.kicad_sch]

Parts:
J4: Sygnały; PinSocket_2x20_P2.54mm_Vertical
J5: Diagnostyka; PinSocket_2x10_P2.54mm_Vertical
J8: Zasilanie+CAN; PinSocket_2x10_P2.54mm_Vertical
R11, R17: 220R; R_0603_1608Metric_Pad0.98x0.95mm_HandSolder
R13, R15: 0R; R_0603_1608Metric_Pad0.98x0.95mm_HandSolder

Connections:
3V3_POT1: R11.1; also elsewhere on the board
3V3_POT2: R13.1; also elsewhere on the board
+5V: J8.2; also elsewhere on the board
+24V: J8.5
CAN-H: J8.6; also elsewhere on the board
CAN-L: J8.8; also elsewhere on the board
CLK: J5.3; also elsewhere on the board
GND: J8.4, J8.7, J8.19, J8.20, R15.1, R17.1; also elsewhere on the board
NRST: J5.5; also elsewhere on the board
unnamed: J8.9, R15.2
unnamed: J8.10, R11.2
unnamed: J8.11, R17.2
unnamed: J8.12, R13.2
SAFETY-IN: J4.8; also elsewhere on the board
SAFETY-OUT: J4.10; also elsewhere on the board
SIG_APPS1: J4.38; also elsewhere on the board
SIG_APPS2: J4.40; also elsewhere on the board
SWD: J5.1; also elsewhere on the board

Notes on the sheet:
OVERTRAVEL
S19
K_OUTPUT0
SWD4
WHEELSPEED2
CLK2
+24F1
PITOT2
SWD5
KILL_PRAWY
BRAKE_PRESSURE2
+24F2
POT_ZAWIAS2
PITOT1
RST4
TEMP1
S36
BSPD_CURRENT
SWD2
K_ANALOG0
S15
SWD3
CLK3
BRAKE_PRESSURE1
TELEMETRIA
KILL_LEWY
WHEELSPEED1
APPS
Z14
S23
RST5
KARTA MOLIK
CLK5
K_OUTPUT2
+5V
K_OUTPUT1
RST3
S25
TIM_IN0
S27

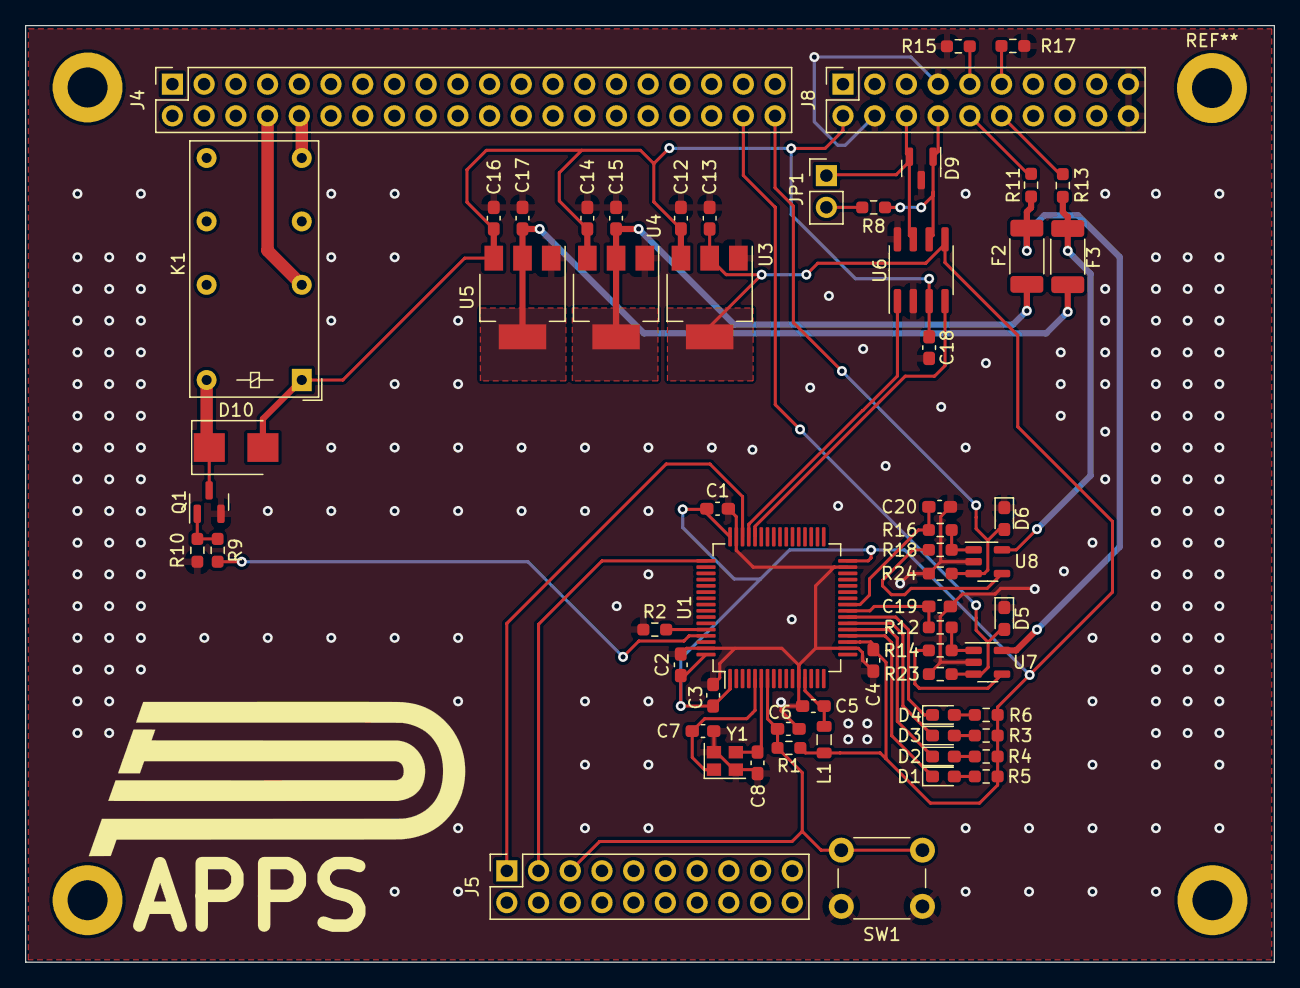
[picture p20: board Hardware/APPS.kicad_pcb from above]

Board: 2 copper layers, 100.0 x 75.0 mm, 62 parts (0 on the bottom side), 44 nets.

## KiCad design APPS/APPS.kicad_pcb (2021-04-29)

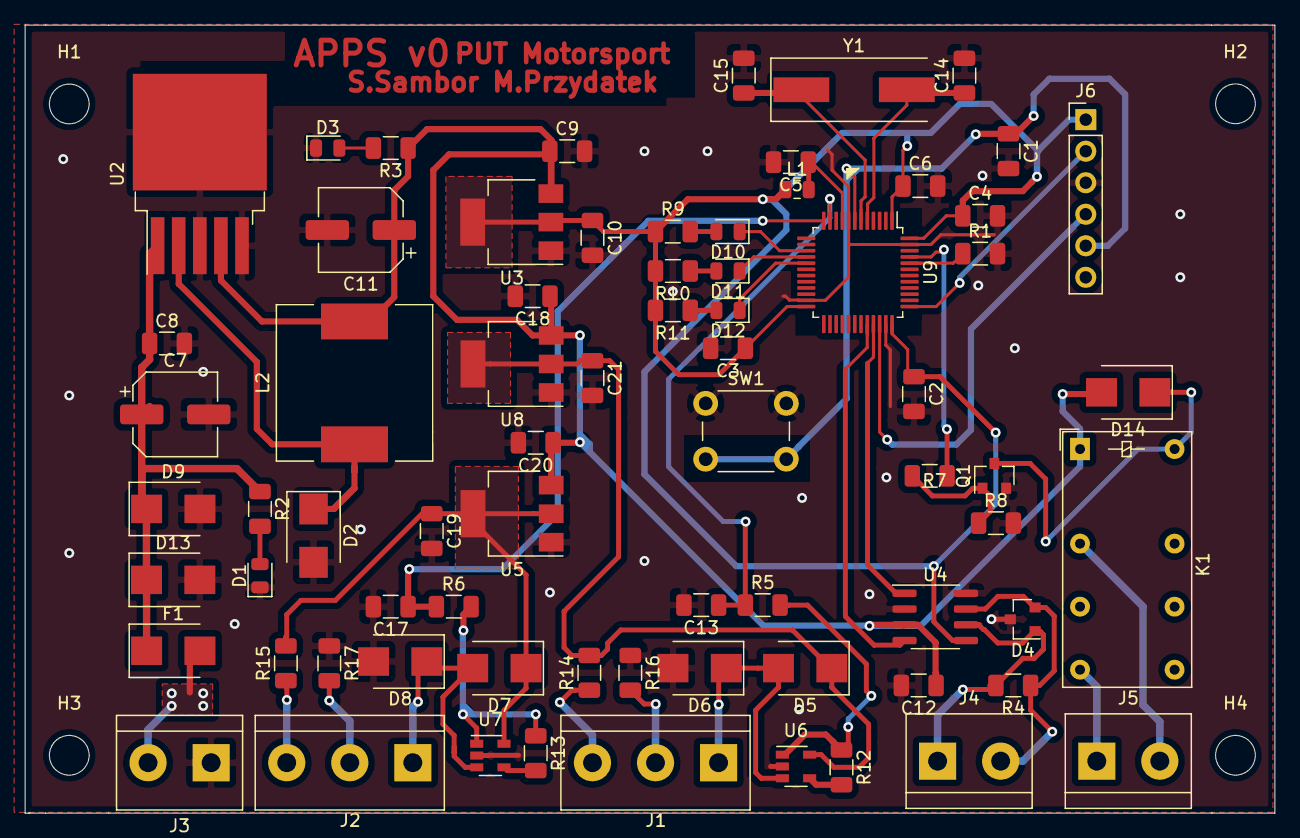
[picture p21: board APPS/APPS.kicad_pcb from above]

Board: 2 copper layers, 100.7 x 63.5 mm, 76 parts (0 on the bottom side), 44 nets.

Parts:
C1, C2, C3, C4, C5, C6, C8, C9, C10, C12, C18, C19, C20, C21: 100nF; C_1206_3216Metric
C7: 100u; CP_Elec_6.3x7.7
C11: 220u; CP_Elec_6.3x7.7
C13, C17: 1uF; C_1206_3216Metric
C14, C15: 22pF; C_1206_3216Metric
D1, D3, D10, D11, D12: LED; LED_0805_2012Metric
D2, D5, D6, D7, D8, D13: D_Schottky; D_SMB
D4: PESD2CAN.215; SOT-23
D9: D_Zener; D_SMB
D14: DIODE; D_SMB
F1: Polyfuse; D_SMB
H1, H2, H3, H4: MountingHole; MountingHole_3.2mm_M3
J1, J2: Screw_Terminal_01x03; TerminalBlock_bornier-3_P5.08mm
J3, J4, J5: Screw_Terminal_01x02; TerminalBlock_bornier-2_P5.08mm
J6: Conn_01x06_Male; PinHeader_1x06_P2.54mm_Vertical
K1: FINDER-30.22; Relay_DPDT_Finder_30.22
L1: L; L_0805_2012Metric
L2: 33u; L_12x12mm_H8mm
Q1: BSS138; SOT-23
R1: R_Small; R_1206_3216Metric
R2, R3, R9, R10, R11: R; R_1206_3216Metric
R4: 120R; R_1206_3216Metric
R5, R6, R12, R13: 300R; R_1206_3216Metric
R7: 100R; R_1206_3216Metric
R8: 10k; R_1206_3216Metric
R14, R15, R16, R17: 0R; R_1206_3216Metric
SW1: SW_Push; SW_PUSH_6mm
U2: LM2596S-5; TO-263-5_TabPin3
U3, U5, U8: LM1117-3.3; SOT-223-3_TabPin2
U4: MCP2562-H-SN; SOIC-8_3.9x4.9mm_P1.27mm
U6, U7: MCP6001-OT; SOT-23-5
U9: STM32F103C8Tx; LQFP-48_7x7mm_P0.5mm
Y1: Crystal 8 MHz; Crystal_SMD_HC49-SD

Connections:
+3.3VA: C21.1, D5.1, R14.2, U6.5, U8.2
+3.3VADC: C19.1, D7.1, R15.2, U5.2, U7.5
+5V: C9.1, C11.1, C12.1, C18.1, C20.1, D14.2, K1.A1, L2.2, R3.1, U2.4, U3.3, U4.3, U5.3, U8.3
+12V: C7.1, C8.1, D9.1, D13.1, F1.1, R2.1, U2.1
Ain0: C13.1, R5.1, U9.11
Ain1: C17.1, R6.1, U9.12
CAN_H: D4.2, J4.2, R4.1, U4.7
CAN_L: D4.1, J4.1, R4.2, U4.6
CAN_RX: U4.4, U9.32
CAN_TX: U4.1, U9.33
EN_RELAY: R7.2, U9.45
NRST: C1.1, J6.5, SW1.2, U9.7
unnamed: C5.1, L1.2, U9.9
unnamed: C14.1, U9.5, Y1.2
unnamed: C15.1, U9.6, Y1.1
unnamed: D1.2, R2.2
unnamed: D2.1, L2.1, U2.2
unnamed: D3.2, R3.2
unnamed: D5.2, D6.1, J1.1, U6.3
unnamed: D7.2, D8.1, J2.1, U7.3
unnamed: D10.1, U9.15
unnamed: D10.2, R9.2
unnamed: D11.1, U9.16
unnamed: D11.2, R10.1
unnamed: D12.1, U9.17
unnamed: D12.2, R11.1
unnamed: D14.1, K1.A2, Q1.3
unnamed: F1.2, J3.2
unnamed: J1.2, R16.2
unnamed: J1.3, R14.1
unnamed: J2.2, R17.2
unnamed: J2.3, R15.1
unnamed: Q1.1, R7.1, R8.1
unnamed: R1.1, U9.44
unnamed: R5.2, R12.1, U6.1
unnamed: R12.2, U6.4
unnamed: R6.2, R13.1, U7.1
unnamed: R13.2, U7.4
SAFETY1: J5.1, K1.14
SAFETY2: J5.2, K1.11
SWCLK: J6.2, U9.37
SWDIO: J6.4, U9.34
SW_GND: C1.2, C2.2, C3.2, C4.2, C5.2, C6.2, C7.2, C8.2, C9.2, C10.2, C11.2, C12.2, C13.2, C14.2, C15.2, C17.2, C18.2, C19.2, C20.2, C21.2, D1.1, D2.2, D3.1, D4.3, D6.2, D8.2, D9.2, D13.2, J3.1, J6.3, Q1.2, R1.2, R8.2, R16.1, R17.1, SW1.1, U2.3, U2.5, U3.1, U4.2, U4.8, U5.1, U6.2, U7.2, U8.1, U9.8, U9.23, U9.35, U9.47
SW_VDDtarget: C2.1, C3.1, C4.1, C6.1, C10.1, J6.1, L1.1, R9.1, R10.2, R11.2, U3.2, U4.5, U9.1, U9.24, U9.36, U9.48

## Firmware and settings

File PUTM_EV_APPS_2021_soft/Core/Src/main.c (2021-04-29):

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
/* Includes ------------------------------------------------------------------*/
#include "main.h"

/* USER CODE BEGIN Includes */
#include <stdlib.h>
#include "APPS_Meta.h"

/* USER CODE END Includes */

ADC_HandleTypeDef hadc1;
DMA_HandleTypeDef hdma_adc1;

CAN_HandleTypeDef hcan;

TIM_HandleTypeDef htim2;
TIM_HandleTypeDef htim3;

UART_HandleTypeDef huart1;

/* USER CODE BEGIN PV */
CAN_FilterTypeDef sFilterConfig;

uint8_t send_CAN_frame;
uint16_t apps_val_raw[100];

uint32_t apps_temp_1 = 0;
uint32_t apps_temp_2 = 0;
uint16_t apps_temp_temp_1 = 0;
uint16_t apps_temp_temp_2 = 0;

uint8_t apps_data[8] = {0, 0, 0, 0, 0, 0, 0, 0};

uint8_t adc_cpl_flag = 0;

float factor_1 = 0.0f;
float factor_2 = 0.0f;

/* USER CODE END PV */

void SystemClock_Config(void);

static void MX_GPIO_Init(void);

static void MX_DMA_Init(void);

static void MX_ADC1_Init(void);

static void MX_CAN_Init(void);

static void MX_TIM2_Init(void);

static void MX_USART1_UART_Init(void);

static void MX_TIM3_Init(void);

/* USER CODE BEGIN PFP */
void My_CAN_init(void);
/* USER CODE END PFP */

/* USER CODE BEGIN 0 */

void HAL_ADC_ConvCpltCallback(ADC_HandleTypeDef *hadc) {
    adc_cpl_flag = 1;
}

/* USER CODE END 0 */

/**
  * @brief  The application entry point.
  * @retval int
  */
int main(void) {
    /* MCU Configuration--------------------------------------------------------*/

    /* Reset of all peripherals, Initializes the Flash interface and the Systick. */
    HAL_Init();

    /* Configure the system clock */
    SystemClock_Config();

    /* Initialize all configured peripherals */
    MX_GPIO_Init();
    MX_DMA_Init();
    MX_ADC1_Init();
    MX_CAN_Init();
    MX_TIM2_Init();
    MX_USART1_UART_Init();
    MX_TIM3_Init();
    /* USER CODE BEGIN 2 */

    CAN_TxHeaderTypeDef tx_header_apps_data;
    tx_header_apps_data.StdId = APPS_CAN_ID;
    tx_header_apps_data.RTR = CAN_RTR_DATA;
    tx_header_apps_data.IDE = CAN_ID_STD;
    tx_header_apps_data.DLC = APPS_CAN_DLC;
    tx_header_apps_data.TransmitGlobalTime = DISABLE;
    uint32_t mail_data_apps = 0;

    factor_1 = (float) (((float) APPS_1_RAW_MAX - (float) APPS_1_RAW_MIN) / (float) APPS_REAL_MAX);
    factor_2 = (float) (((float) APPS_2_RAW_MAX - (float) APPS_2_RAW_MIN) / (float) APPS_REAL_MAX);

    // INIT OTHER STUFF

    // Turn on safety
    HAL_GPIO_WritePin(SAFETY_GPIO_Port, SAFETY_Pin, 1);

    My_CAN_init();

    HAL_ADC_Start_DMA(&hadc1, (uint32_t *) apps_val_raw, 100);
    HAL_TIM_Base_Start(&htim3);
    HAL_TIM_Base_Start_IT(&htim2);

    HAL_GPIO_WritePin(LED_1_GPIO_Port, LED_1_Pin, 1);
    HAL_GPIO_WritePin(LED_2_GPIO_Port, LED_2_Pin, 1);
    HAL_GPIO_WritePin(LED_3_GPIO_Port, LED_3_Pin, 1);
    /* USER CODE END 2 */

    /* Infinite loop */
    /* USER CODE BEGIN WHILE */


    while (1) {
        if (send_CAN_frame == 1 && adc_cpl_flag == 1) {
            send_CAN_frame = 0;
            adc_cpl_flag = 0;

            apps_temp_1 = 0;
            apps_temp_2 = 0;

            for (int i = 0; i < 100; i = i + 2) {
                apps_temp_1 += apps_val_raw[i];
                apps_temp_2 += apps_val_raw[i + 1];
            }

            apps_temp_1 = apps_temp_1 / 50;
            apps_temp_2 = apps_temp_2 / 50;
            /*
             * check if APPS is not broken:
             * 	- apps_read < APPS_RAW_MIN - 100
             * 	- apps_read > APPS_RAW_MAX + 100
             *
             * */

            if (apps_temp_1 < APPS_1_RAW_MIN || apps_temp_2 < APPS_2_RAW_MIN) {
                apps_temp_1 = APPS_REAL_MIN;
                apps_temp_2 = APPS_REAL_MIN;
            } else if (apps_temp_1 > APPS_1_RAW_MAX || apps_temp_2 > APPS_2_RAW_MAX) {
                apps_temp_1 = APPS_REAL_MAX;
                apps_temp_2 = APPS_REAL_MAX;
            } else {
                apps_temp_1 = (uint16_t) ((float) (apps_temp_1 - APPS_1_RAW_MIN) / factor_1);
                apps_temp_2 = (uint16_t) ((float) (apps_temp_2 - APPS_2_RAW_MIN) / factor_2);
            }

            apps_temp_temp_1 = apps_temp_1;
            apps_temp_temp_2 = apps_temp_2;

            // TODO change magic number
            if ((abs(apps_temp_2 - apps_temp_1)) > apps_temp_1 * 0.1) {
                apps_temp_1 = 0;
                apps_temp_2 = 0;
                HAL_GPIO_WritePin(LED_1_GPIO_Port, LED_1_Pin, 0);
            }
            else{
                HAL_GPIO_WritePin(LED_1_GPIO_Port, LED_1_Pin, 1);
            }

            if (apps_temp_1 > APPS_REAL_MAX)
                apps_temp_1 = APPS_REAL_MAX;

            if (apps_temp_2 > APPS_REAL_MAX)
                apps_temp_2 = APPS_REAL_MAX;

            apps_data[0] = (uint8_t) (apps_temp_1 & 0x00FF);
            apps_data[1] = (uint8_t) (apps_temp_1 >> 8);
            HAL_CAN_AddTxMessage(&hcan, &tx_header_apps_data, apps_data, &mail_data_apps);


            while (HAL_CAN_IsTxMessagePending(&hcan, mail_data_apps));
            apps_data[0] = 0;
            apps_data[1] = 0;
        }


        /* USER CODE END WHILE */

        /* USER CODE BEGIN 3 */
    }
    /* USER CODE END 3 */
}

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
/* USER CODE BEGIN 4 */

void My_CAN_init(void) {
    sFilterConfig.FilterBank = 0;
    sFilterConfig.FilterMode = CAN_FILTERMODE_IDMASK;
    sFilterConfig.FilterScale = CAN_FILTERSCALE_32BIT;
    sFilterConfig.FilterIdHigh = 0x0000;
    sFilterConfig.FilterIdLow = 0x0000;
    sFilterConfig.FilterMaskIdHigh = 0x0000;
    sFilterConfig.FilterMaskIdLow = 0x0000;
    sFilterConfig.FilterFIFOAssignment = CAN_RX_FIFO0;
    sFilterConfig.FilterActivation = ENABLE;
    sFilterConfig.SlaveStartFilterBank = 14;

    if (HAL_CAN_ConfigFilter(&hcan, &sFilterConfig) != HAL_OK) {
        Error_Handler();
    }

    if (HAL_CAN_Start(&hcan) != HAL_OK) {
        Error_Handler();
    }

    if (HAL_CAN_ActivateNotification(&hcan, CAN_IT_RX_FIFO0_MSG_PENDING | CAN_IT_TX_MAILBOX_EMPTY) != HAL_OK) {
        Error_Handler();
    }
}
/* USER CODE END 4 */
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


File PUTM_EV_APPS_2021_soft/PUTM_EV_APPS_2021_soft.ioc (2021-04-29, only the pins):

Mcu.UserName=STM32F103C8Tx
PA1.Signal=ADCx_IN1
PA10.Signal=USART1_RX
PA11.Signal=CAN_RX
PA12.Signal=CAN_TX
PA13.Signal=SYS_JTMS-SWDIO
PA14.Signal=SYS_JTCK-SWCLK
PA2.Signal=ADCx_IN2
PA5.GPIO_Label=LED_1
PA5.Signal=GPIO_Output
PA6.GPIO_Label=LED_2
PA6.Signal=GPIO_Output
PA7.GPIO_Label=LED_3
PA7.Signal=GPIO_Output
PA9.Signal=USART1_TX
PB8.GPIO_Label=SAFETY
PB8.Signal=GPIO_Output
PD0-OSC_IN.Signal=RCC_OSC_IN
PD1-OSC_OUT.Signal=RCC_OSC_OUT

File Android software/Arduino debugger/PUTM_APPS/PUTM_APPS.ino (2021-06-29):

int in1 = A0;
int in2 = A1;
int Incoming_value = 0;
int del = 100;

void setup() {
  Serial.begin(9600);
  pinMode(in1,INPUT);
  pinMode(in2,INPUT);
  pinMode(11, OUTPUT);
  pinMode(12, OUTPUT); 
  pinMode(13, OUTPUT);  
}

void loop() {
  //Map the value from 10 bits to 8 bits:
  
  byte val1 = map(analogRead(in1),0,1024.0,0,255);
  byte val2 = map(analogRead(in2),0,1024.0,0,255);
  byte a[] = {val1, val2};
  Serial.write(a, 2);
  delay(del);

    if(Serial.available() > 0) {
      
    Incoming_value = (Serial.read());      
     
    if(Incoming_value == 'a'){             
      digitalWrite(13, HIGH);
      digitalWrite(12, LOW);
      digitalWrite(11, LOW);
    } else if(Incoming_value == 'b') {      
      digitalWrite(13, LOW); 
      digitalWrite(12, HIGH);
      digitalWrite(11, LOW);
    }else if(Incoming_value == 'c') {     
      digitalWrite(13, LOW); 
      digitalWrite(12, LOW);
      digitalWrite(11, HIGH);
    }
    
    if(Incoming_value < 90){
      del = (Incoming_value - 48) * 10;
    }
  }      
}

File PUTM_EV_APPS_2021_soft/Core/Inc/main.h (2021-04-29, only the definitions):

#define LED_1_Pin GPIO_PIN_5
#define LED_1_GPIO_Port GPIOA
#define LED_2_Pin GPIO_PIN_6
#define LED_2_GPIO_Port GPIOA
#define LED_3_Pin GPIO_PIN_7
#define LED_3_GPIO_Port GPIOA
#define SAFETY_Pin GPIO_PIN_8
#define SAFETY_GPIO_Port GPIOB

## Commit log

2020-12-06 init commit with soft- and hard-ware
    [APPS.kicad_pcb, APPS.sch, CAN.sch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]
2020-12-06 CAN 500, should not work
    [PUTM_EV_APPS_2021_soft.ioc, main.c]
2020-12-08 check analog input if it is correctly calibrated
    [main.c]
2021-03-19 updated timers
2021-04-21 Added files from remote work
    [APPS.kicad_pcb, APPS.sch, AnalogInputs.sch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]
2021-04-21 Changed PCB edhes shape
    [APPS.kicad_pcb]
2021-04-21 Deleted mounting holes from schematic (now on pcb edgecuts)
    [Connectros.sch]
2021-04-22 Positioned Bluetooth module
    [APPS.kicad_pcb, APPS.sch, AnalogInputs.sch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]
2021-04-22 Updated BT position
    [APPS.kicad_pcb]
2021-04-27 Changed HC-05 pins for other Forbot HC-05
    [APPS.kicad_pcb, APPS.sch, BluetoothModule.sch]
2021-04-27 Quick fixes
    [APPS.kicad_pcb, APPS.sch]
2021-04-27 handling error - difference beetween sensors is too big
    [main.c]
2021-04-27 Added sensors' error handler If difference is too big it should be measurement should be 0
    [PUTM_EV_APPS_2021_soft.ioc, main.c]
2021-04-29 New boundaries, error handlers
    [main.c]
2021-05-06 Updated buttons position
2021-05-07 Arduino code for debugging Android Studio App
2021-05-07 Added PUT Motorsport Icon (All possible formats)
2021-05-10 PCB router 50%
    [APPS.kicad_pcb, APPS.sch, AnalogInputs.sch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]
2021-05-10 Components labels placed
    [APPS.kicad_pcb, APPS.sch, AnalogInputs.sch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]
2021-05-10 Added Logos library, PCB FINISHED
    [APPS.kicad_pcb]
2021-05-19 GitIgnore update
    [APPS.kicad_pcb]
2022-01-07 Changed footprints and PCB layout. Schematic cleanup.
    [APPS.kicad_sch, AnalogInputs.kicad_sch, BluetoothModule.kicad_sch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]
2022-01-07 Schematic cleanup and description
    [APPS.kicad_sch]
2022-01-07 PCB layout and routing
    [APPS.kicad_pcb, APPS.kicad_sch, Connectros.kicad_sch]
2022-01-10 Deleted 24V section
2022-01-13 Changed crystal footprint, fixed capactiors, added debug LED
    [APPS.kicad_pcb, APPS.kicad_sch, PowerModule.kicad_sch]
2022-01-13 Fixed CAN lines to be equal length
    [APPS.kicad_pcb, APPS.kicad_sch]
2022-01-13 Schematic cleanup
    [APPS.kicad_pcb, APPS.kicad_sch, AnalogInputs.kicad_sch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]
2022-01-14 Generated BOM
    [APPS.csv, APPS.kicad_pcb, APPS.kicad_sch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]
2022-01-19 Switch STM capacitors' positions, added mounting
    [APPS.kicad_pcb]

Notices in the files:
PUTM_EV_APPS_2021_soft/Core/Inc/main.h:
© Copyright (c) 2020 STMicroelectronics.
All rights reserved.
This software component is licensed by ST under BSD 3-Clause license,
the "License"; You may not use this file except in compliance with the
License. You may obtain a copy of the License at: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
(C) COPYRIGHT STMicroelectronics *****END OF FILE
